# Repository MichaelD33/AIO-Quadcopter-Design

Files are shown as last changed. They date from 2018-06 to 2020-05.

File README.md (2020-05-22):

# AIO Quadcopter Design Files

__Disclaimer:__ This is a functional *yet unfinished* project. The information in this repository is provided without warranty or guaranteed funtionality. If you attempt to replicate this project, I am not responsible for any damages or failures associated with your work.

--- 

## This repository contains:

### 1. The schematics and Gerber files for the AIO quadcopter circuit board.

### 2. The 3D printed frame for the AIO quadcopter circuit board 
- (*version 0.4.1 strongly recommended*)

### 3. The Fusion360 assembly file for the AIO quadcopter.

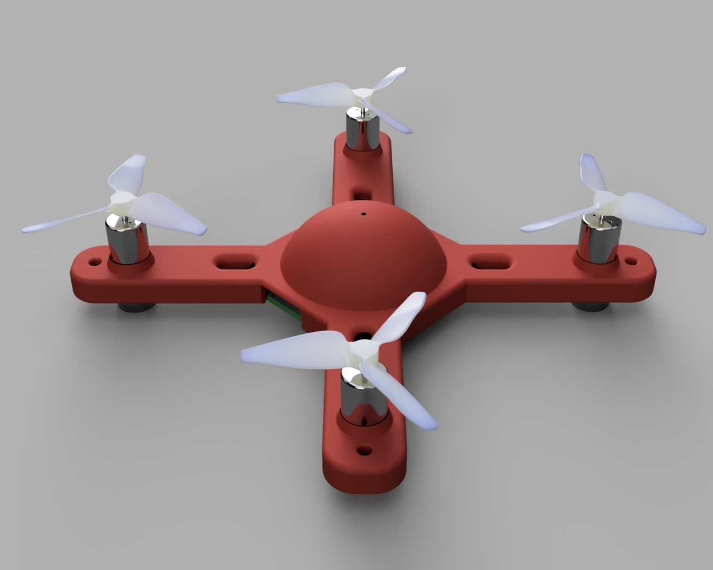
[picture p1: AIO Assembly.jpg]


### 4. The test jig folder containing all of the 3D printed parts necessary to build a test stand for the AIO quadcopter (version 0.3 and later) 
- (*The single axis version is strongly recommended over the legacy model*)
- This test stand is designed to operate using this [single axis control program](https://github.com/MichaelD33/SingleAxisController).

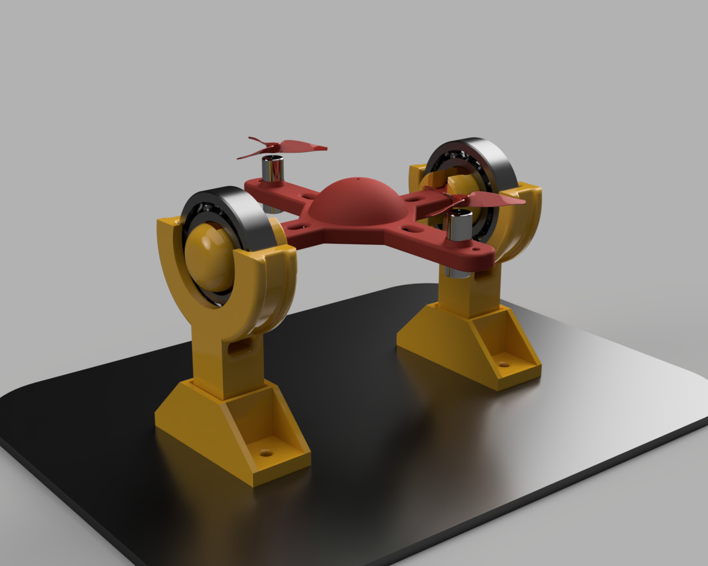
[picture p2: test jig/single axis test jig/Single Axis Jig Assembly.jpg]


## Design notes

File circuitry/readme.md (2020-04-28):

# AIO Quadcopter Circuit Board Design File Directory:

---

### Note: The use of the [AIO Quadcopter version 0.4.1](https://github.com/MichaelD33/AIO-Quadcopter-Design/tree/master/circuitry/version%200.4.1) circuit board design is highly recommended for new users attempting to follow this project.

*Prototype legacy designs are provided for reference only!*

---

## Version 0.4.1:



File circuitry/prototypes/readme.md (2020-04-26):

# AIO Quadcopter Legacy PCB Design Directory:

---

### Warning: This is a directory for archived designs. No further work will be done with these designs. Functionality or compatibility with future AIO designs is not ensured.

*These designs are provided as reference. The use of these designs is not recommended to anyone attempting this project.*

The use of the [AIO Quadcopter version 0.4.1](https://github.com/MichaelD33/AIO-Quadcopter-Design/tree/master/circuitry/version%200.4.1) 
circuit board design is highly recommended for new users attempting to follow this project.

---

## Directory Overview

### non-functional prototypes
	- Original PCB designs.
	- Used for early code development and hardware testing

### Version 0.3
	- First working revision of the PCB - This design removed the 5v buck/boost converter to decrease the overall weight; however, this resulted in the center of gravity being significantly offset from the center of the PCB. This results in a number of issues with the device's balance.

### Version 0.4
	- Fixed center of gravity
	- Replaced the 5V regulator (decreased efficiency due to the 3.3V regulator being powered by the 5V reg.)
	
### Version 0.4.1 (see link above)
	- Added flyback diode and reverse polarity protection mosfet.
	- 5V regulator and output pads (3.3V regulator still powered via 5V line)

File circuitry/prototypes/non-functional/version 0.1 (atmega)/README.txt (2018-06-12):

/* VERSION 1.0 README */

While the first circuit board design ultimately functioned, it required a number of modifications and did not satisfy my expectations for power consumption and efficiency. In addition, the motor drivers on this version of the quadcopter design came in a BGA package and were incredibly tiny and required significant patience and skill to properly solder. Finally, I also encountered issues with isolating the USB power from battery power which caused a number of issues later on when attempting to interface over serial or program the flight controller.

For these reasons, I would not recommend fabricating this version of the quadcopter. I have included it in the library for documentation purposes only.

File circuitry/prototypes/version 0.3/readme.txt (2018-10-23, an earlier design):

In an attempt to decrease the number of parts on the quadcopter circuit board, I removed the 5v regulator and connected the atmega directly to the 1S lipo voltage supply. In this process I changed the center of gravity significantly enough to offset the battery placement onto the arms. For this reason I would suggest working with version 0.4 over this iteration.

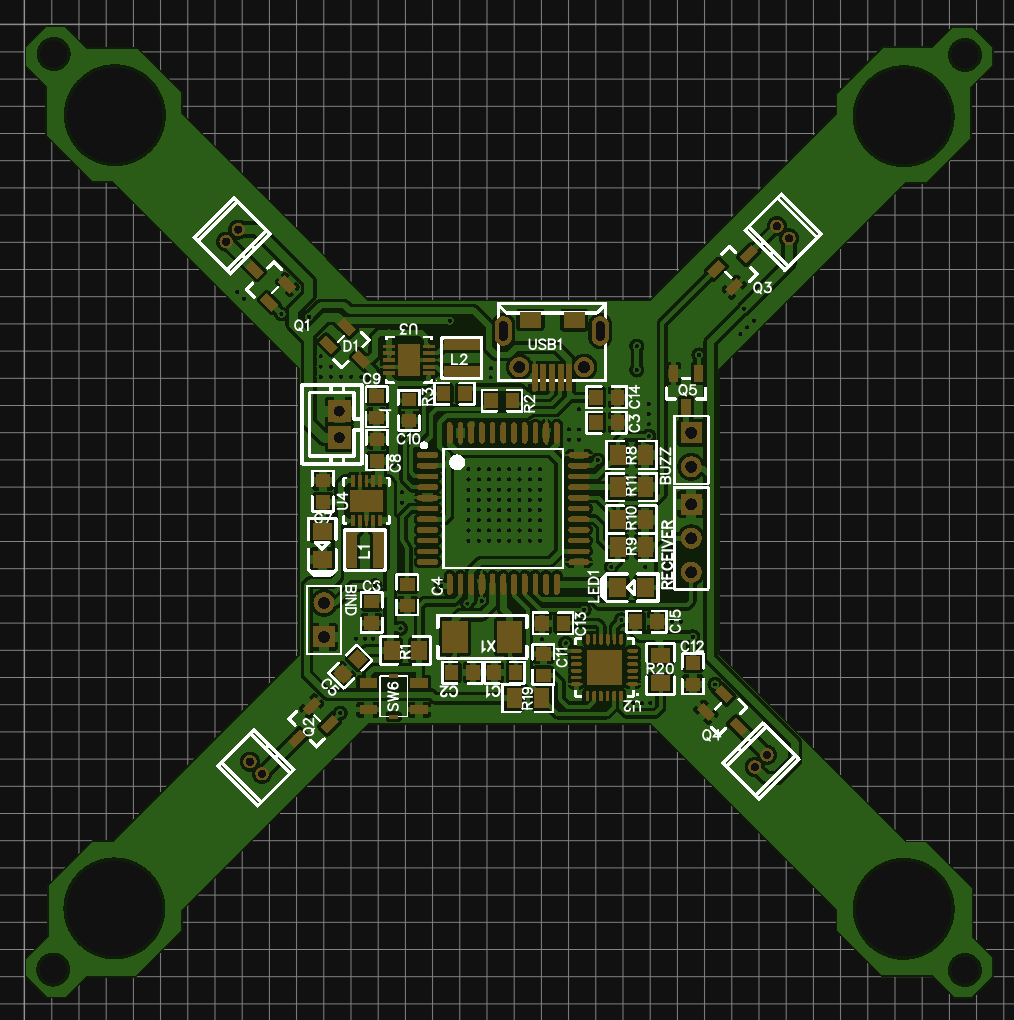
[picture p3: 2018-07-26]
circuitry/prototypes/version 0.4/AIO_32u4_v0.4.png

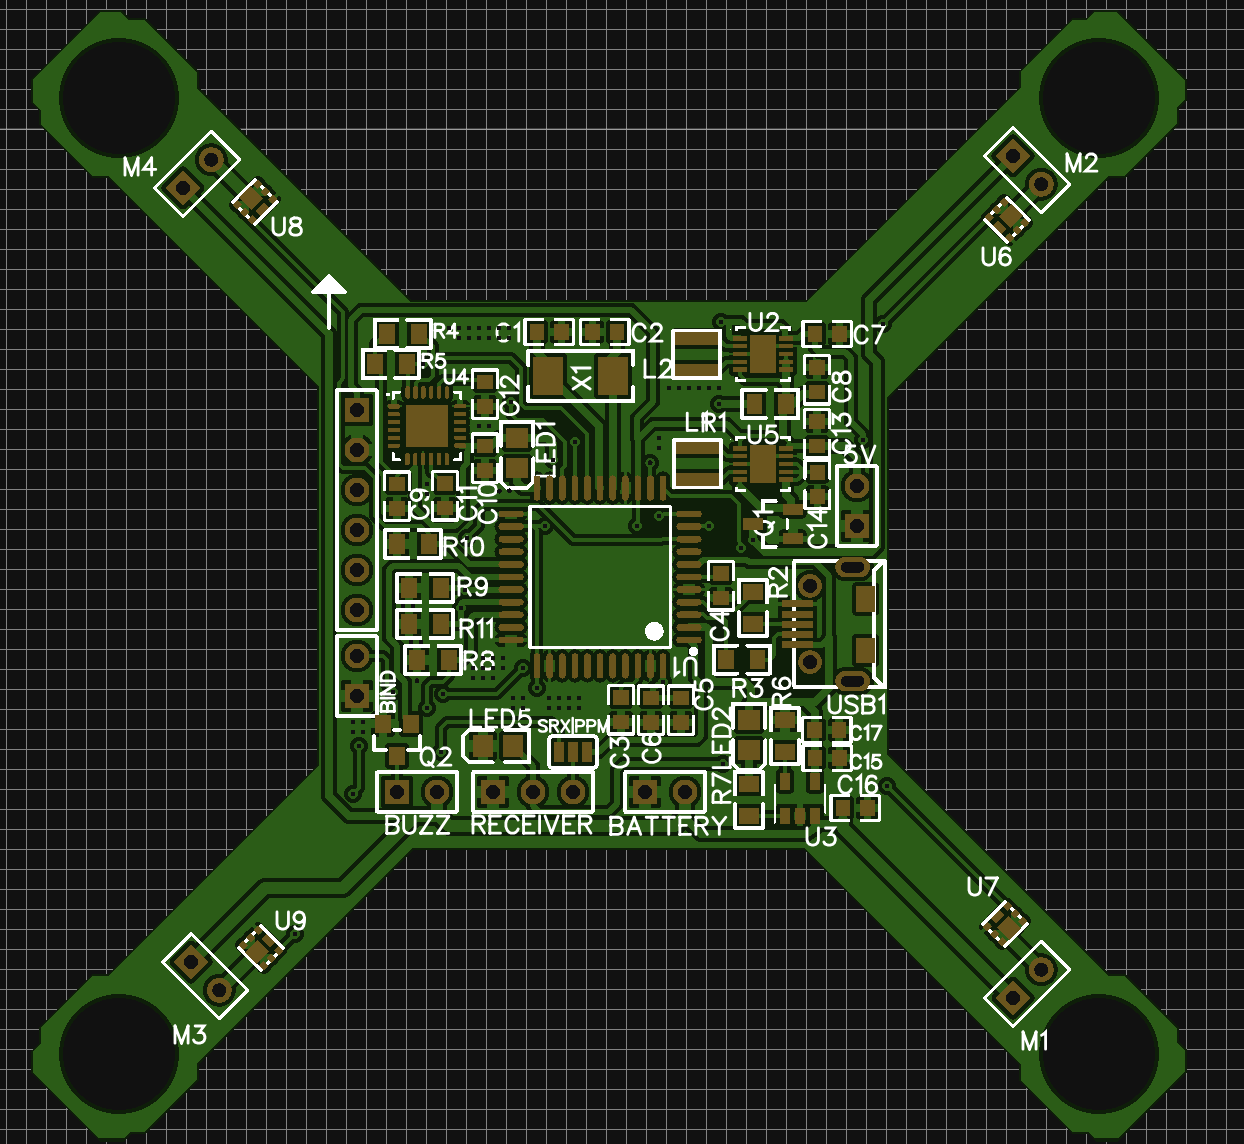
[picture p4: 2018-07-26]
circuitry/prototypes/non-functional/version 0.1 (atmega)/AIO_32u4_v0.1.png

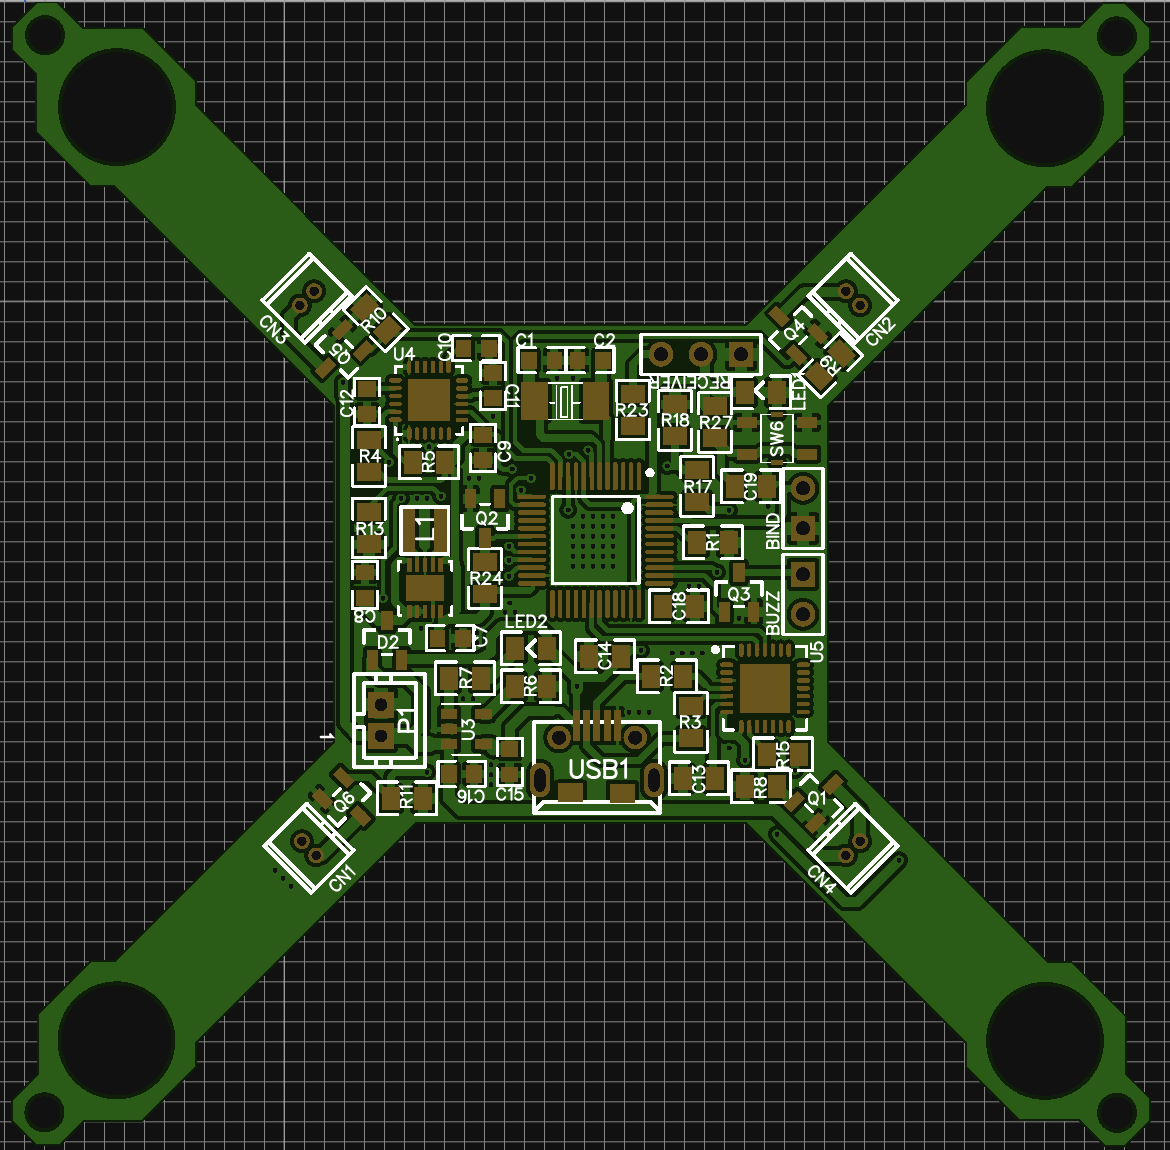
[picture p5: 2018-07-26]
circuitry/prototypes/non-functional/version 0.2 (stm32)/AIO_stm32_v0.2.png

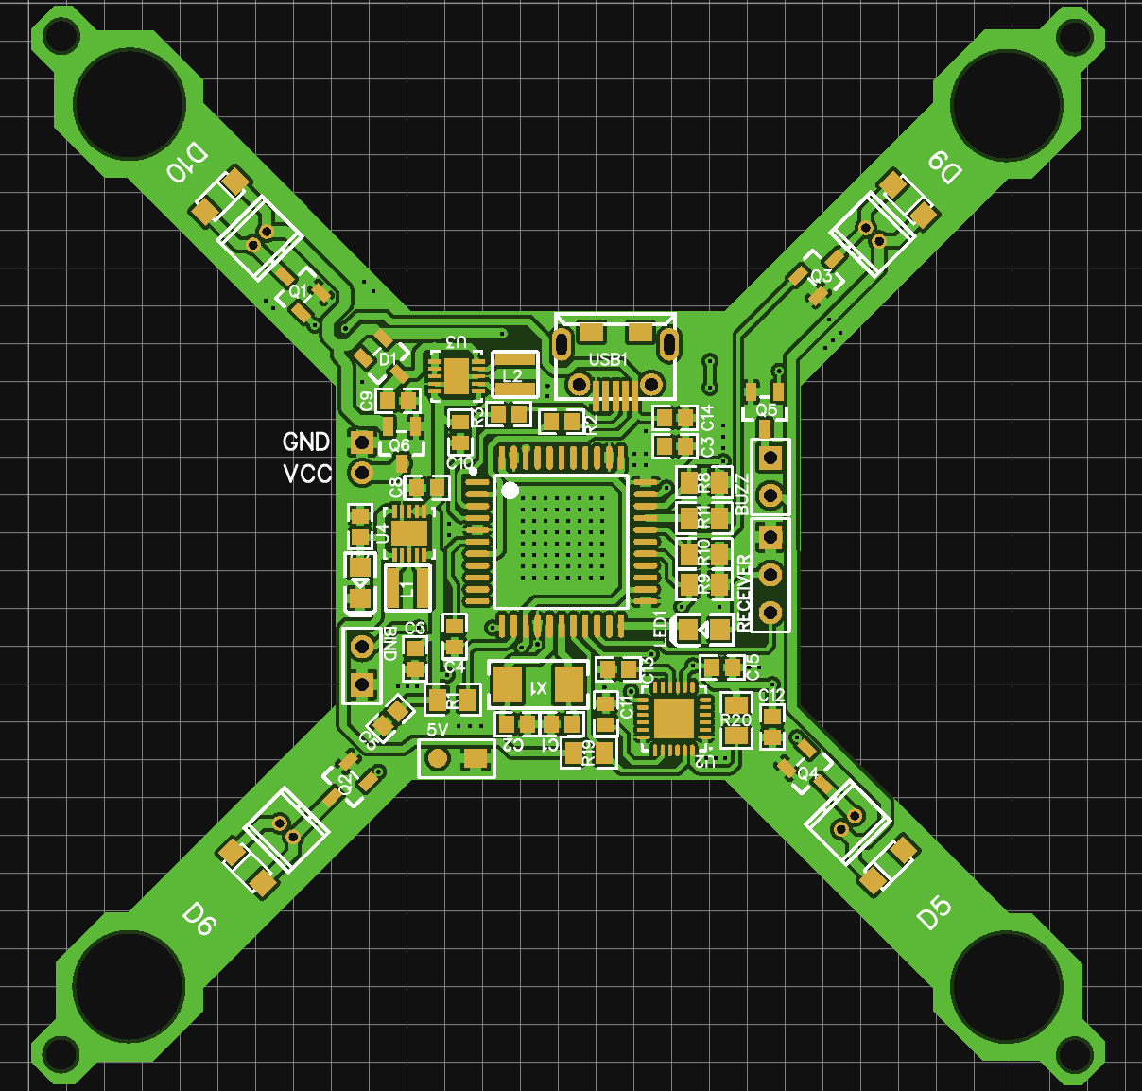
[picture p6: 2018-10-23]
circuitry/version 0.4.1/AIO_32u4_v0.4.1.png

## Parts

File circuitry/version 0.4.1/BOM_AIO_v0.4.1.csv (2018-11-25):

ID | Name | Designator | Footprint | Quantity | Manufacturer Part | Manufacturer | Supplier | Supplier Part | Mounted | LCSC Assembly
1 | ATMEGA32U4-AU | U1 | QFP-44_10X10X08P | 1 | ATMEGA32U4-AU | ATMEL | LCSC | C44854 | Yes
2 | 22pf | C1,C2 | 0603' | 2 | ? |  |  |  | Yes
3 | 10k | R1,R19,R20,R10,R11,R8,R9 | 0805' | 7 | ? |  |  |  | Yes
4 | 0.1uf | C3,C12,C13 | 0603' | 3 | ? |  |  |  | Yes
5 | 1uf | C4,C5,C6,C14 | 0603' | 4 | ? |  |  |  | Yes
6 | 16MHz | X1 | OSC-YSX-5032_2P | 1 | X503216MSD2GI | YXC | LCSC | C73355 | Yes
7 | MPU6050 | U2 | QFN-24_4X4X05P | 1 | MPU6050 | InvenSense | LCSC | C24112 | Yes | Yes
8 | 0.01uf | C15 | 0603' | 1 | ? |  |  |  | Yes
9 | 2.2nf | C11 | 0603' | 1 | ? |  |  |  | Yes
10 | TPS63001DRCR | U4 | DRC10-2400X1650TP | 1 | ? |  |  |  | Yes
11 | NR3015T2R2M | L1,L2 | 3.0*3.0*1.5MM | 2 | NR3015T2R2M | TAIYO YUDEN | LCSC | C86423 | Yes
12 | 10uf | C7,C8,C10,C9 | 0603' | 4 | ? |  |  |  | Yes
13 | E6C0805UR | LED3,LED1 | LED-0805 | 2 | E6C0805UR | LCSC | LCSC | C2295 | Yes
14 | TPS63002DRCR | U3 | DRC10-2400X1650TP | 1 | ? |  |  |  | Yes
15 | MICRO USB 5S B | USB1 | MICRO-USB-1 | 1 | micro USBFemale | ValuePro | LCSC | C10418 | Yes
16 | Buzzer | BUZZ | HDR-2X1/2.54 | 1 | Header-Male-2.54_1x2 | LCSC | LCSC | C36717 | Yes
17 | RECEIVER | RECEIVER | HDR-3X1/2.54 | 1 | Header-Male-2.54_1x3 | LCSC | LCSC | C49257 | Yes
18 | BIND | BIND | HDR-2X1/2.54 | 1 | Header-Male-2.54_1x2 | LCSC | LCSC | C36717 | Yes
19 | SI2302CDS-T1-E3 | Q4,Q2,Q3,Q1 | SOT-23(SOT-23-3) | 4 | SI2302CDS-T1-E3 | VISHAY | LCSC | C141544 | Yes
20 | 1.25T-2P-DP | CN4,CN2,CN3,CN1 | 1.25T-2P-DP | 4 | 1.25T-2P-DP | HRO | LCSC | C145940 | Yes
21 | BAT54C | D1 | SOT-23(SOT-23-3) | 1 | BAT54C | CJ | LCSC | C2135 | Yes
22 | MMBT3906LT1G | Q5 | SOT-23(SOT-23-3) | 1 | MMBT3906LT1G | ON | LCSC | C53444 | Yes
23 | 22 | R2,R3 | 0603' | 2 | ? |  |  |  | Yes
24 | S07J-GS08 or | S07M-GS08 | D2,D3,D4,D5 | DO-219AB | 4 | S07J-GS08 | VISHAY | LCSC | C145004 | Yes
25 | Header-Male-2.54_1x2 | 5V | HDR-2X1/2.54 | 1 | 826629-2 | TE Connectivity | LCSC | C86471 | Yes
26 | SI2301CDS-T1-GE3 | Q6 | SOT-23(SOT-23-3) | 1 | SI2301CDS-T1-GE3 | VISHAY | LCSC | C10487 | Yes | Yes
27 | VCC | VCC,GND | _PIN | 2 | New SchematicLib |  |  | undefined | Yes

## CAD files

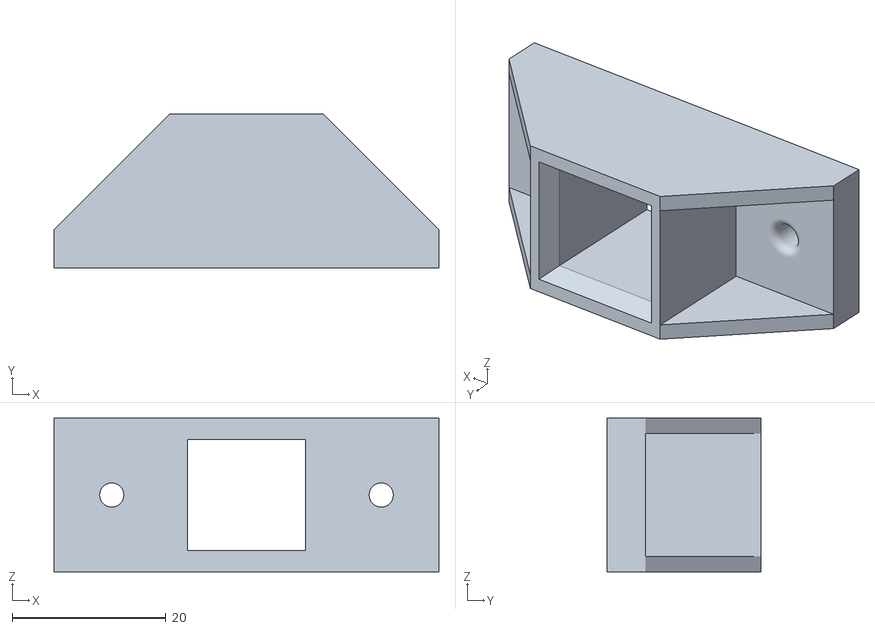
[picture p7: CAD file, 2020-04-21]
test jig/single axis test jig/Base Mount.stl
50.0 x 20.0 x 20.0

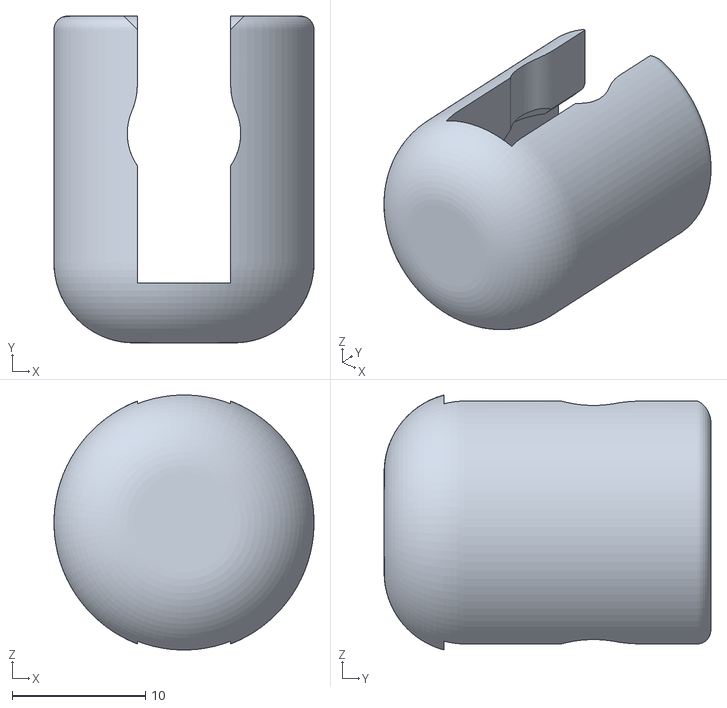
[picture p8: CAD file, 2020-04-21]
test jig/single axis test jig/Bearing Clip.stl
19.5 x 24.5 x 19.1

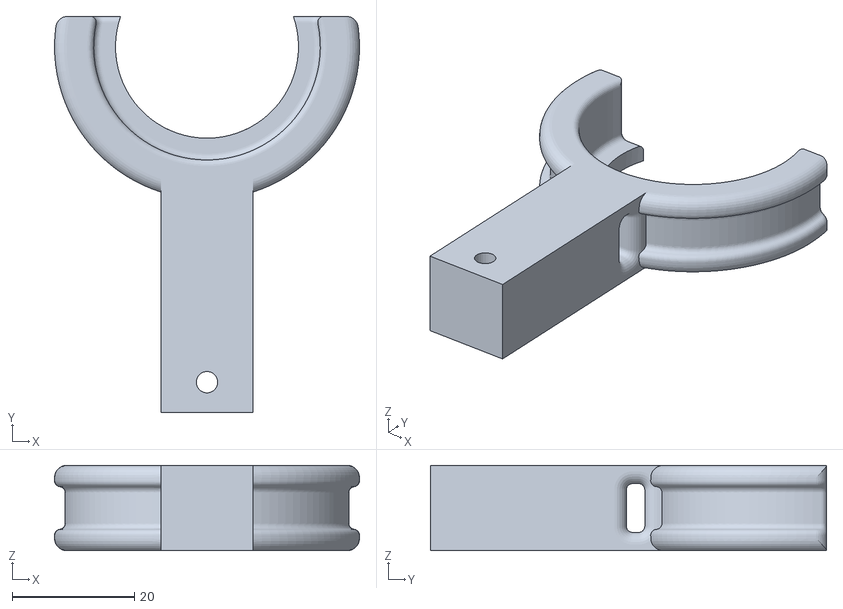
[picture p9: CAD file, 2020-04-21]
test jig/single axis test jig/Mounting Post.stl
50.0 x 65.0 x 14.0

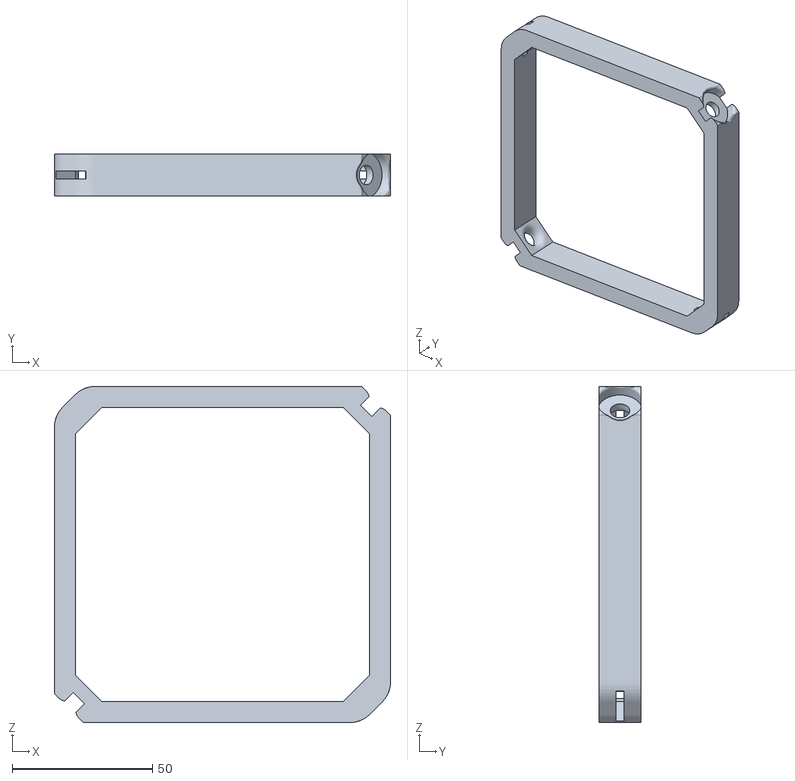
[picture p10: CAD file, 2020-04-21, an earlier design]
test jig/legacy test jig/Full Mount Test.stl
120.0 x 15.0 x 120.0

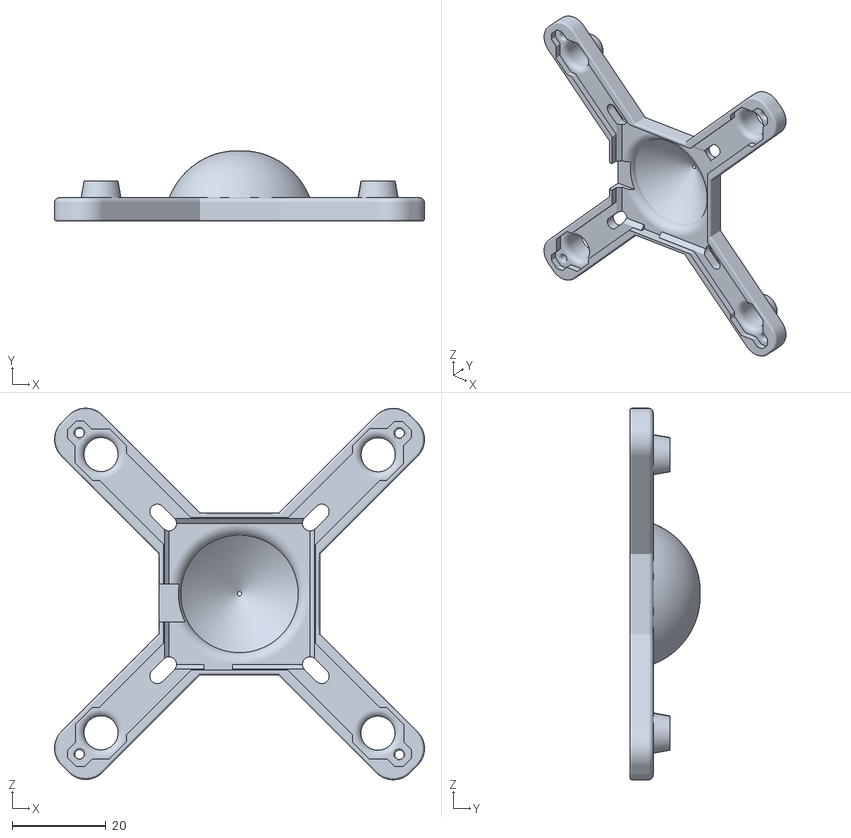
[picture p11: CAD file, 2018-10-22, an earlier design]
3D printed frame/legacy designs/AIO Top Mount Frame v1.stl
78.8 x 15.0 x 79.1

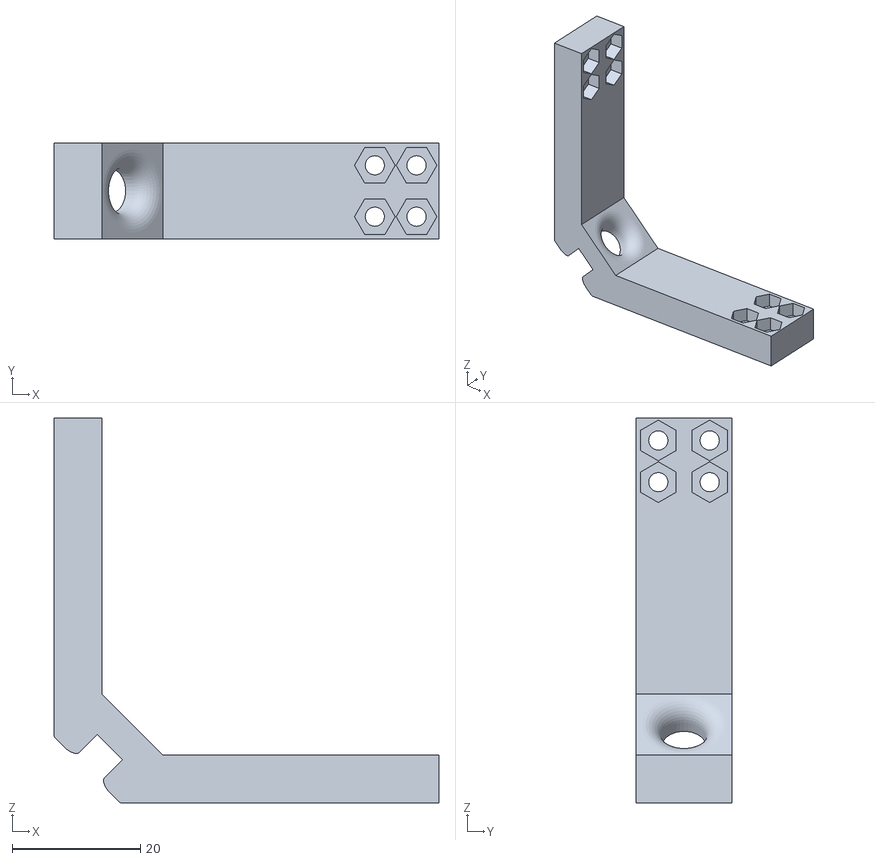
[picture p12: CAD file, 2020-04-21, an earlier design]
test jig/legacy test jig/Large Corner Bracket - Dual.stl
60.0 x 15.0 x 60.0

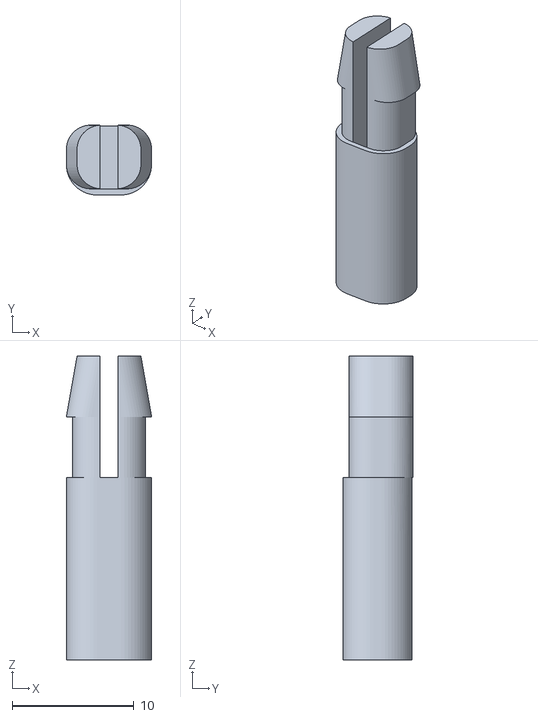
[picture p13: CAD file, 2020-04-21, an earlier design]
test jig/legacy test jig/quadcopterMountingClip_Bearing.stl
7.01 x 5.75 x 25.0

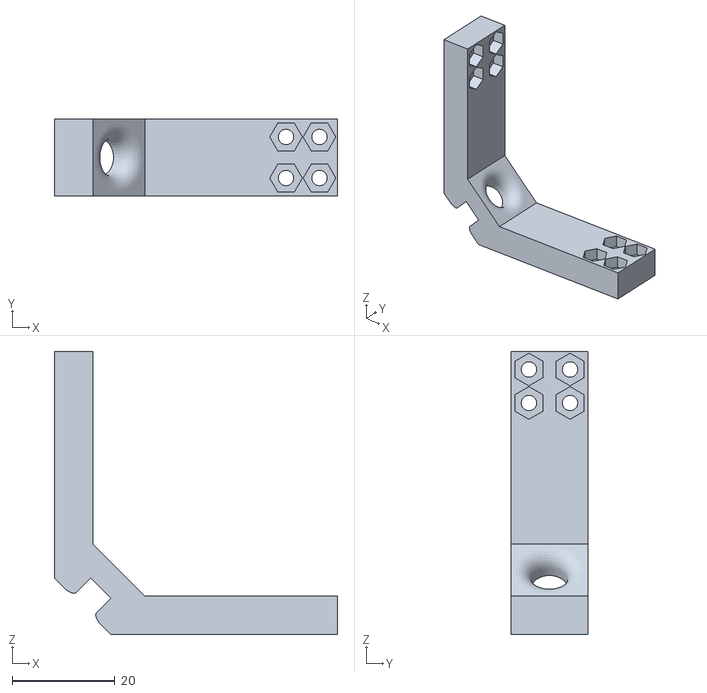
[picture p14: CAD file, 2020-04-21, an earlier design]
test jig/legacy test jig/Corner Bracket Dual Mounting Hole.stl
55.0 x 15.0 x 55.0

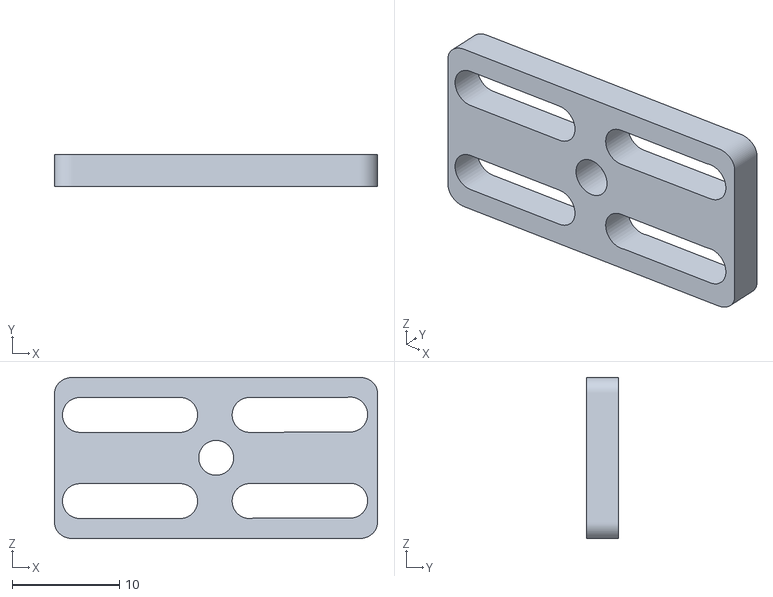
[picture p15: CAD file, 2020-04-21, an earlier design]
test jig/legacy test jig/Expanding Bracket.stl
30.1 x 3.00 x 15.0

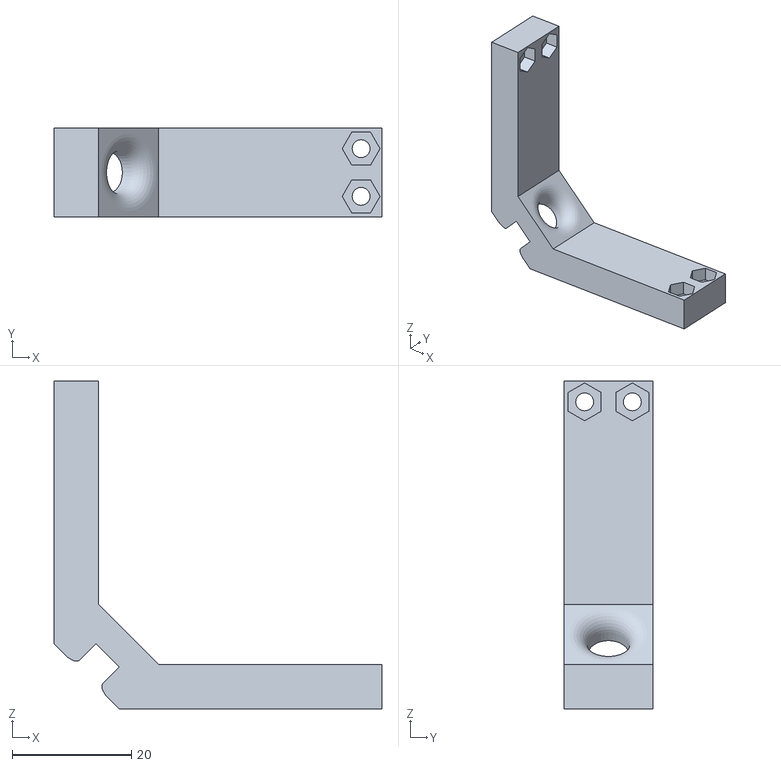
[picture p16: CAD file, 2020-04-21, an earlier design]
test jig/legacy test jig/PID Expanding Mount.stl
55.0 x 15.0 x 55.0

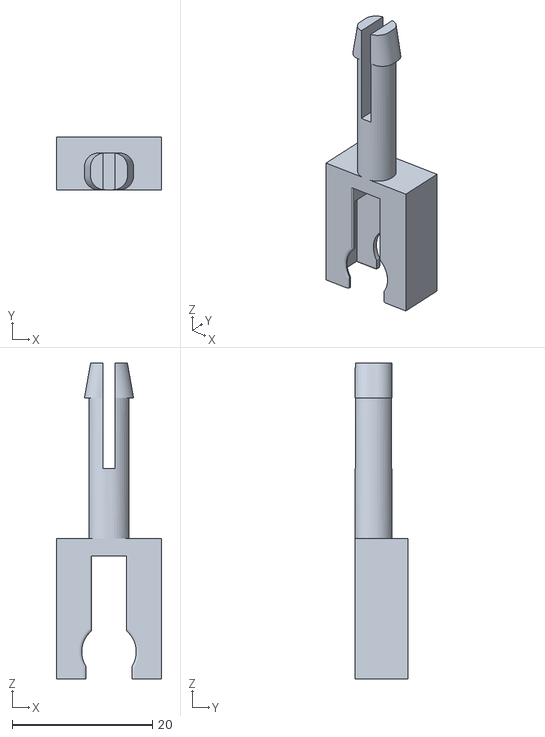
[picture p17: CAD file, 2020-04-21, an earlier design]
test jig/legacy test jig/innerAxisMountingPin.stl
15.0 x 7.50 x 45.0

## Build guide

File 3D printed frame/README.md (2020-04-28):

# AIO 3D Printed Frame

---

This 3D printed frame serves as support for the AIO quadcopter PCB. 
The frame was added for two main purposes: vibration dampening and rigidity.

Assembly:

- The quadcopter frame is attached to the PCB using standard [M2 x 6mm](https://www.mcmaster.com/92000a013) screws. 
These screws attach to the quadcopter PCB through the mounting holes at the end of each motor arm. 
The screws are held in place using [M2 nuts](https://www.mcmaster.com/93800a300).

- The frame also features cutouts for vibration dampening components. 



- [M2 O-Rings](https://www.banggood.com/20-PCS-O-rings-Vibration-Isolation-Flight-Controller-Protection-Rubber-Band-Green-White-for-RC-Drone-p-1174651.html?ID=521800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)
or [M2 O-Rings – Option 2](https://www.mcmaster.com/9262k568)

- [Adhesive Foam Pads](https://www.banggood.com/10Pcs-URUAV-3M-Double-Sided-Foam-Adhesive-Tapes-Pad-Square-Strip-for-Gyro-RC-Models-p-1353765.html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)
or [Adhesive Foam – Option 2](https://www.mcmaster.com/75785t13)

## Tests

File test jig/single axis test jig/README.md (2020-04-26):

# Single Axis Test Jig Design



---

This testing jig is designed to allow the quadcopter to move freely along a singular axis of rotation. 
This setup configuration allows for the user to test the quadcopter's behavior and tune the PID controller without the
quadcopter flying away. Addionally, given that the motion is restricted to a singular axis, PID tuning is simplified by only focusing
on the singular axis of rotation (as opposed to the legacy test jig design, which allows for movement on all axes when properly configured).

---

__Dependancies:__

- This jig requires two of each 3D printed component, one set for each arm of the quadcopter. 

- Two bearings are also required for the device to be to rotate freely along the axis of rotation. The test jig is designed to work with [20x37 mm bearings](https://www.mcmaster.com/5972k168).

- Mounting the quadcopter circuit board to the jig requires the 3D printed [AIO frame](https://github.com/MichaelD33/AIO-Quadcopter-Design/blob/master/3D%20printed%20frame/AIO%20Frame%20Refined.stl).

- Finally, of course, the [AIO quadcopter circuit board](https://github.com/MichaelD33/AIO-Quadcopter-Design/tree/master/circuitry/version%200.4.1) is required— this is the main control board for the quadcopter.

---

__Program Changes:__

- This setup utilizes a custom control program to test and tune the quadcopter. This program may be found in the [SingleAxisController](https://github.com/MichaelD33/SingleAxisController/) repository.

Read more about the specific changes on the single axis controller repository.

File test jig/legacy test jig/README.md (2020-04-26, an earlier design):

# Legacy Test Jig

---

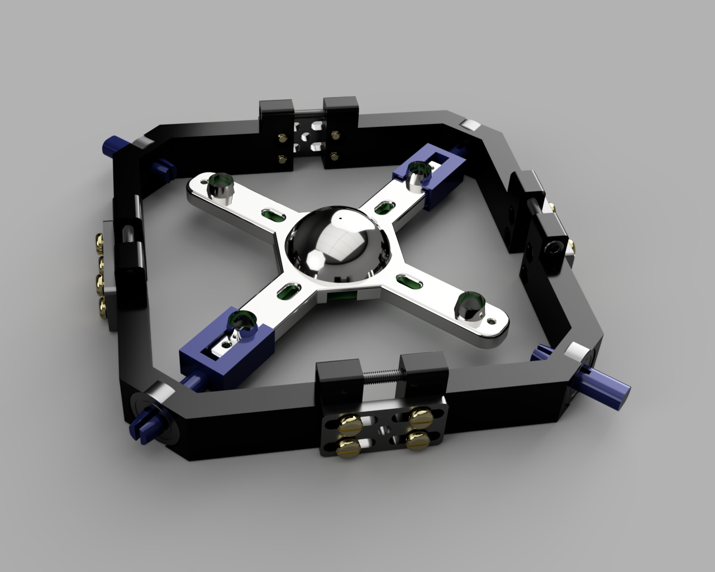
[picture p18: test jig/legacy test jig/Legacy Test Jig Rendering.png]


### Warning: This is an archived design. No further work will be done with this design. Compatibility with future AIO designs is not ensured.

*These designs are provided as reference. The use of these designs is not recommended to anyone attempting this project on their own.*

### Design update: 

The use of the [Single Axis Test Jig](https://github.com/MichaelD33/AIO-Quadcopter-Design/tree/master/test%20jig/single%20axis%20test%20jig) 
design is highly recommended for new users attempting to follow this project.

---

__Purpose:__

The creation of this test jig is described in an article I published on the [Ultimaker website](https://ultimaker.com/learn/how-the-tools-we-use-influence-the-designs-we-make)— 
see: "__Tools in testing__".

The quadcopter uses information from the sensors to calculate how fast to spin the motors in order to move to 
a certain location. This process is handled by an algorithm known as a PID controller. Before the quadcopter can fly, this controller needs to be configured through laborious testing, and figuring out where 
to start can be fairly daunting. Furthermore, the guess-and-check method usually causes the quadcopter to go crashing into the 
wall. This caused me to wonder, how might I control and analyze the movement of the quadcopter without it flying away and 
crashing into the wall?

Introducing, the testing jig. This contraption allows the user to test the quadcopter without worrying that the device will break
from colliding with the wall. 

[See an example of this test jig in action](http://delaney.nyc/wp-content/uploads/2020/04/PIDTestJig3.gif)

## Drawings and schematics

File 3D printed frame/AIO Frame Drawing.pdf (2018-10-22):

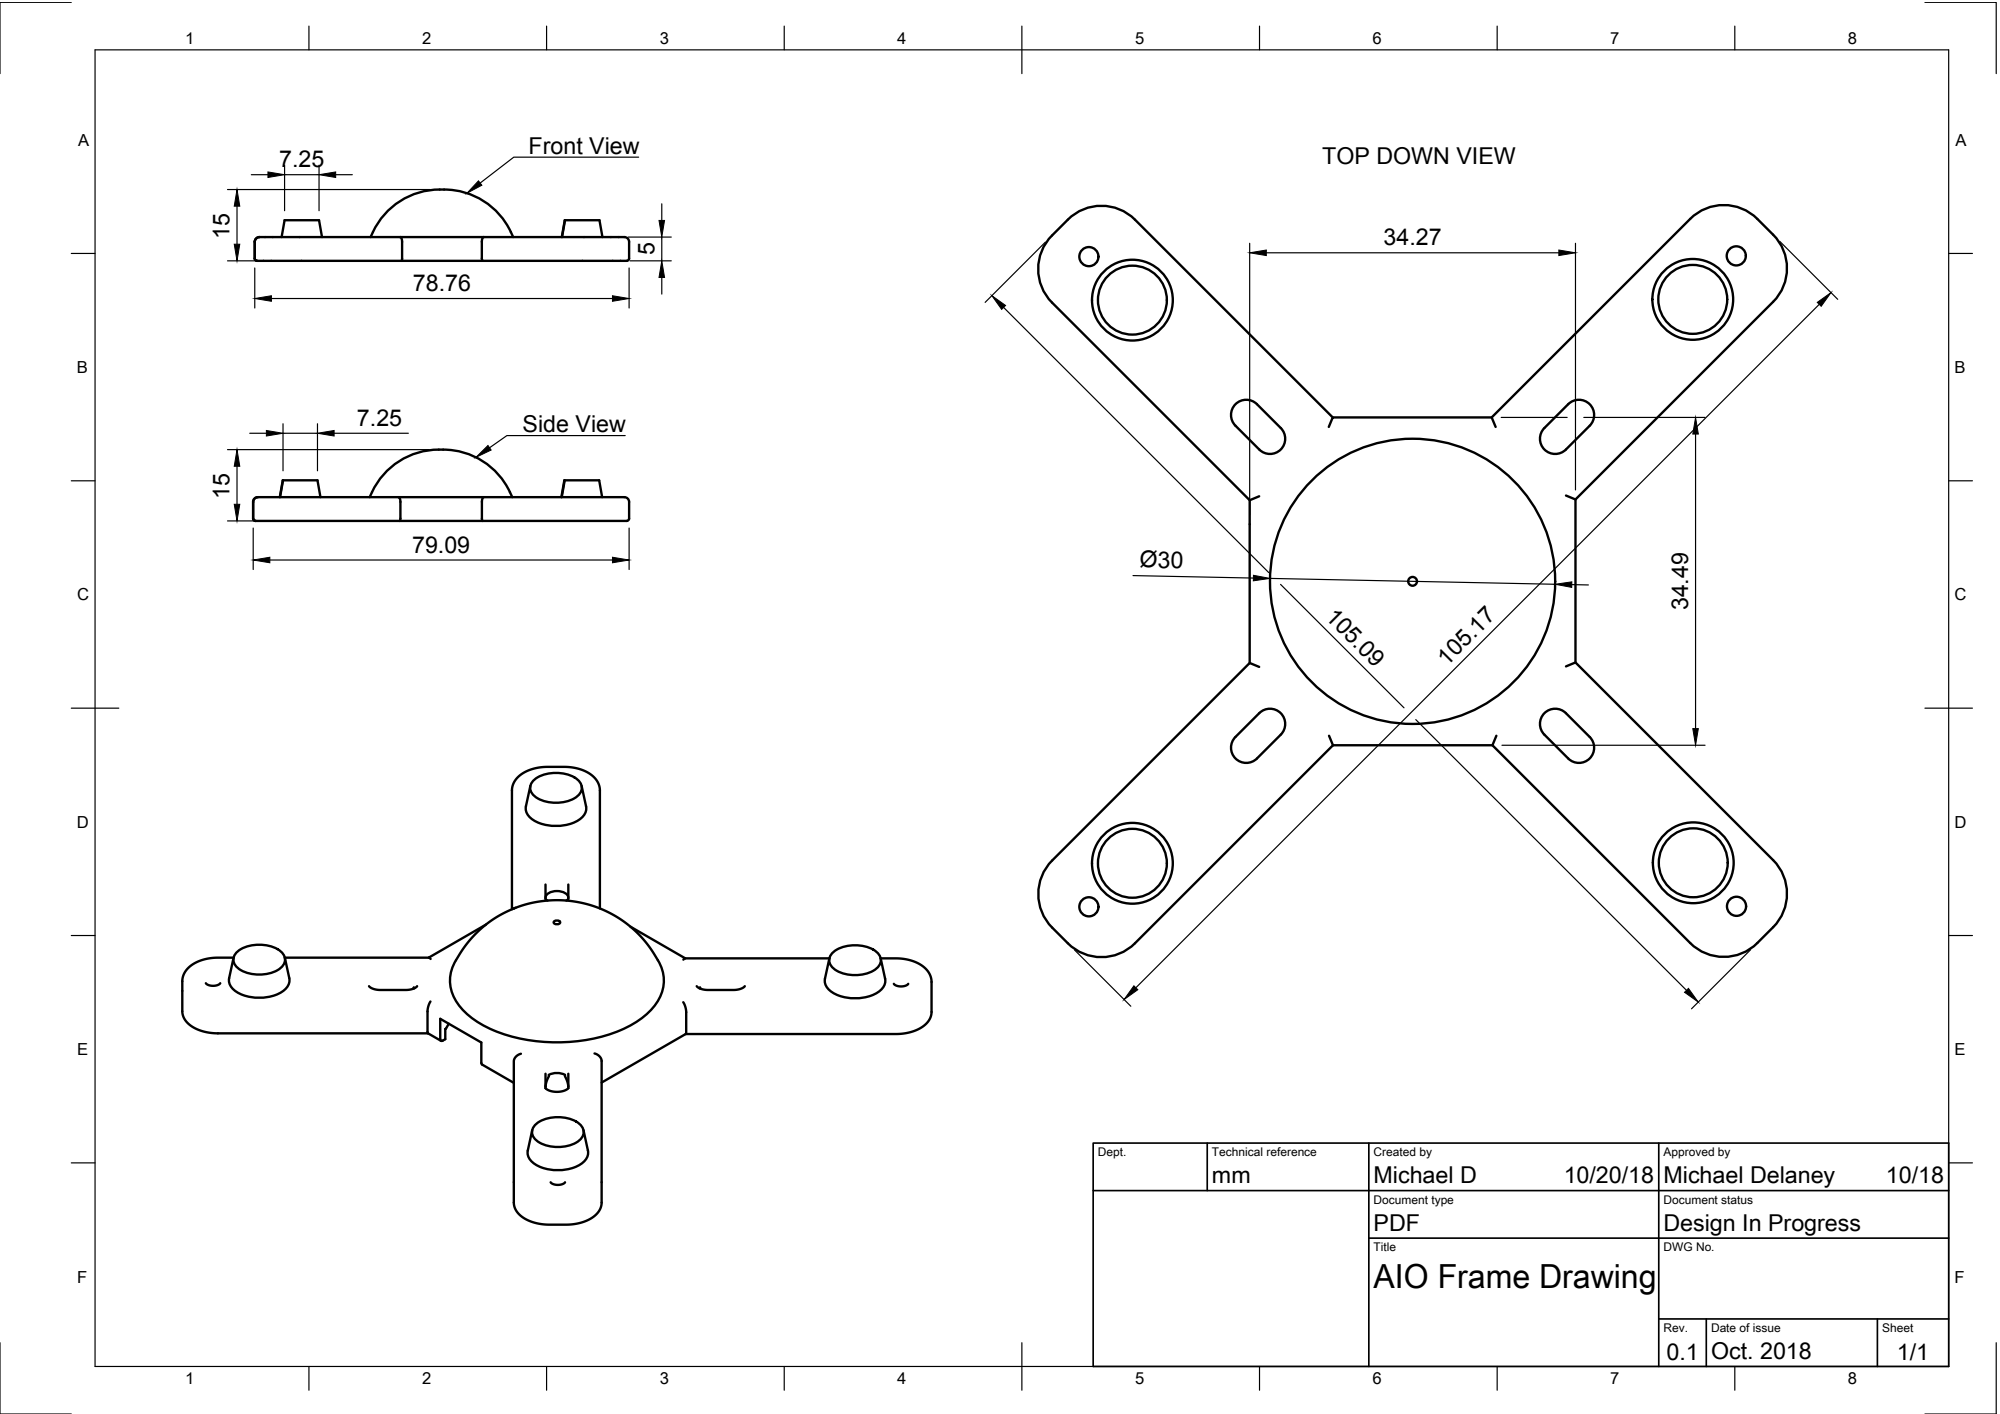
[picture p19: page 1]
Front View; Side View

TOP DOWN VIEW

Dept. | Technical reference mm | Created by Michael D 10/20/18 | Approved by Michael Delaney 10/18

Document type PDF | Document status Design In Progress

Title AIO Frame Drawing | DWG No.

Rev. 0.1 | Date of issue Oct. 2018 | Sheet 1/1

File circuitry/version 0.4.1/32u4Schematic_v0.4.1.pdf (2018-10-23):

+3.3V +3.3V

## VCC

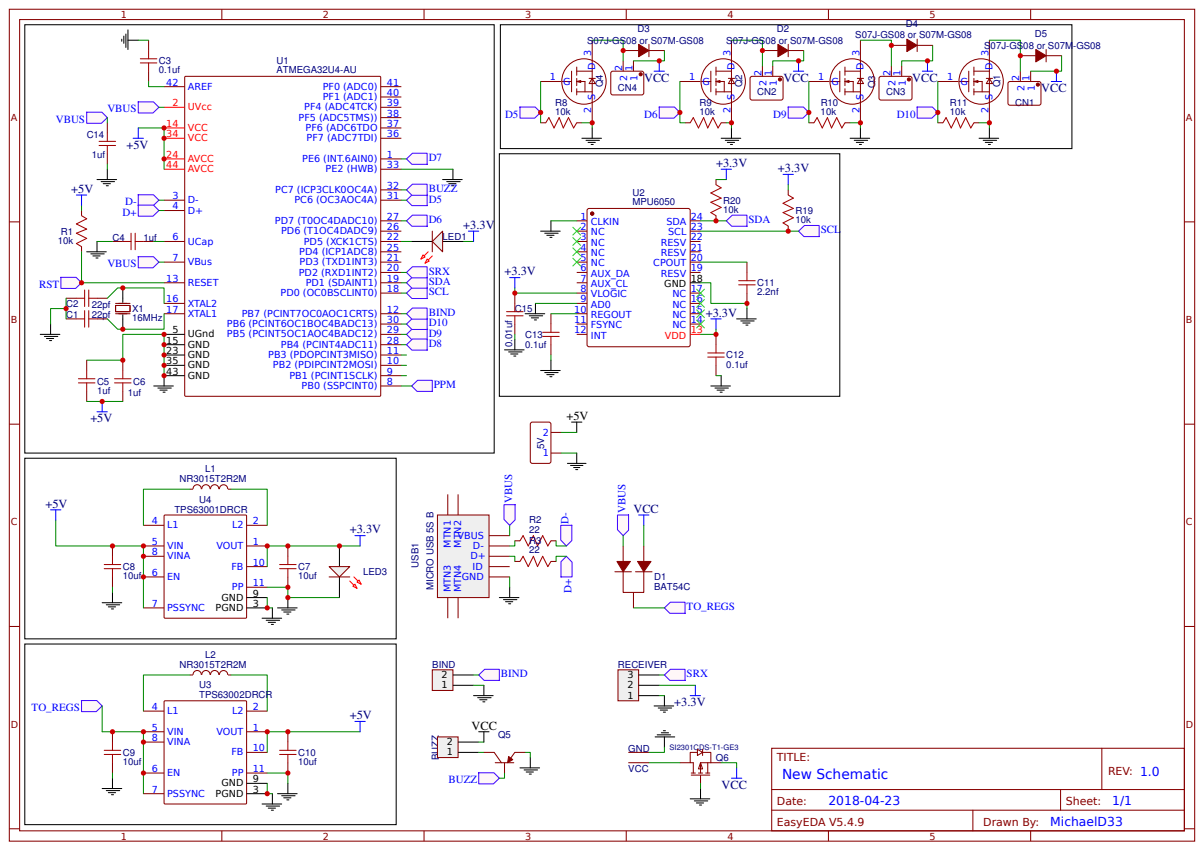
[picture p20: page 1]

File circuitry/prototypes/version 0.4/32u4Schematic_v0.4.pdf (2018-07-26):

+3.3V +3.3V

## VCC

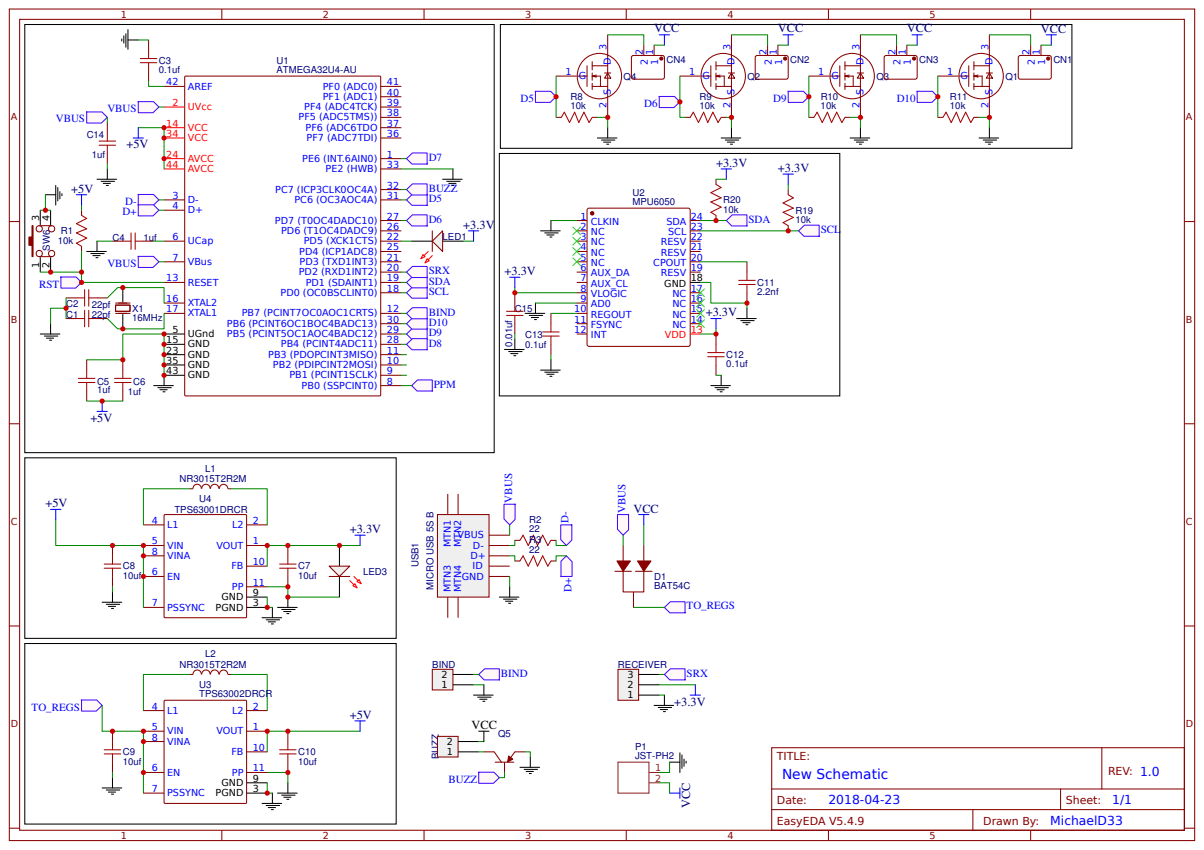
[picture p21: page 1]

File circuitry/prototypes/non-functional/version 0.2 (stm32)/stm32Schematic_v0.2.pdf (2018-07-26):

## MPU6050

U4

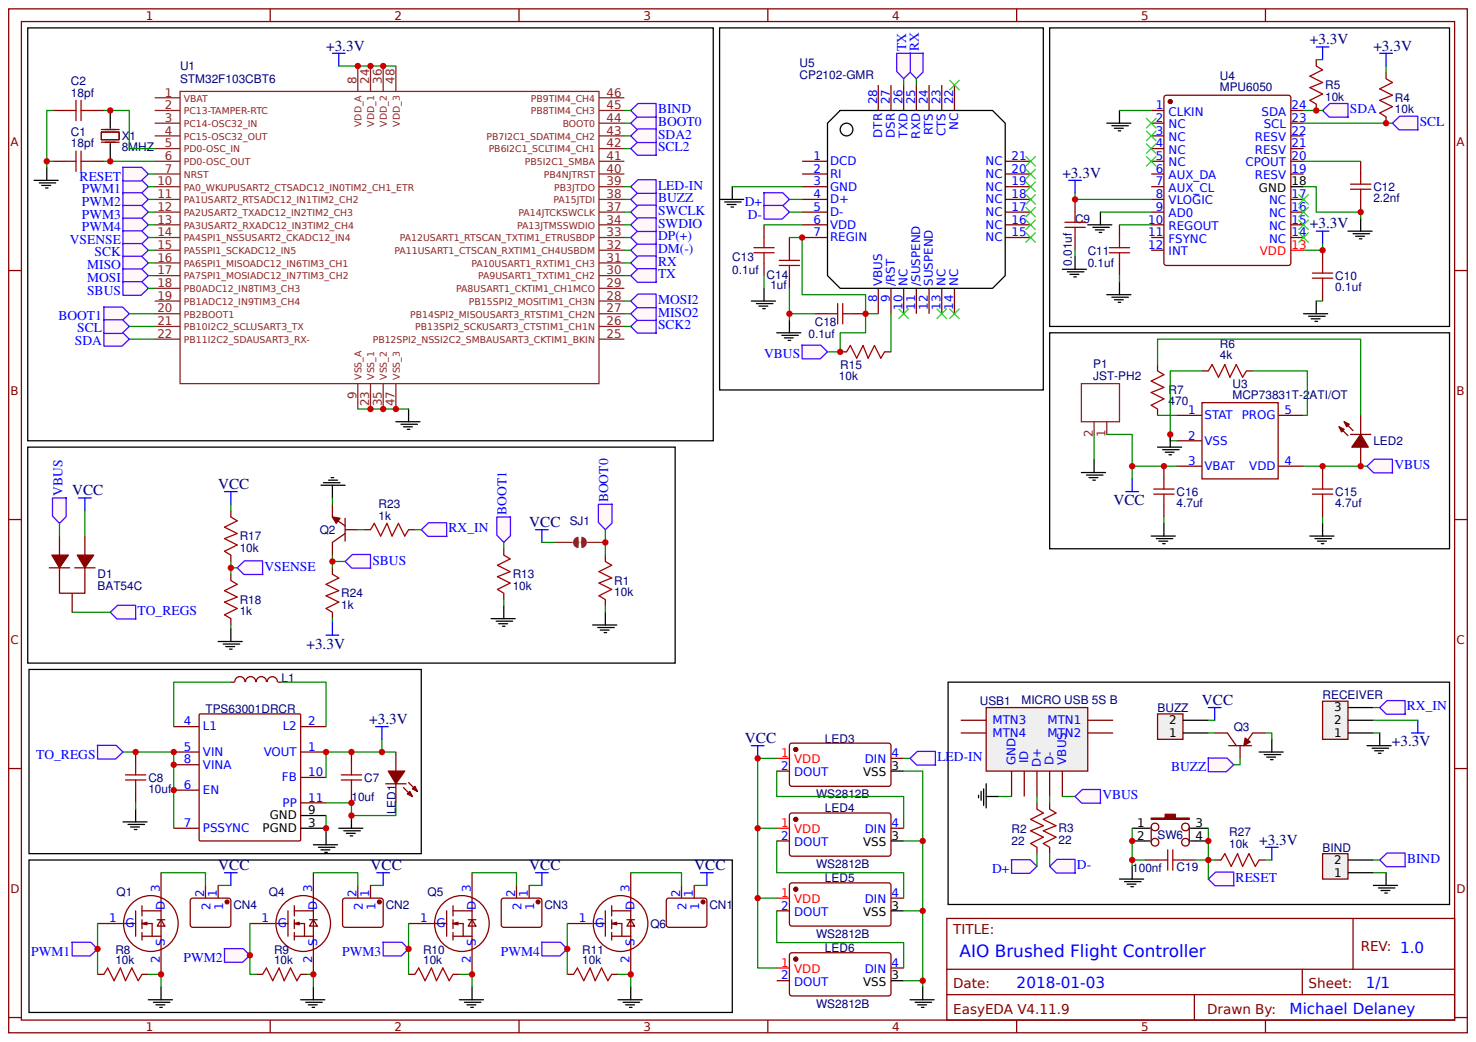
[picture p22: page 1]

NC 22 CTS 23 RTS 24 RXD 25 TXD 26 DSR 27 DTR 28

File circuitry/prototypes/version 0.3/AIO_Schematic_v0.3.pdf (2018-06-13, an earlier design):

+3.3V +3.3V

## VCC

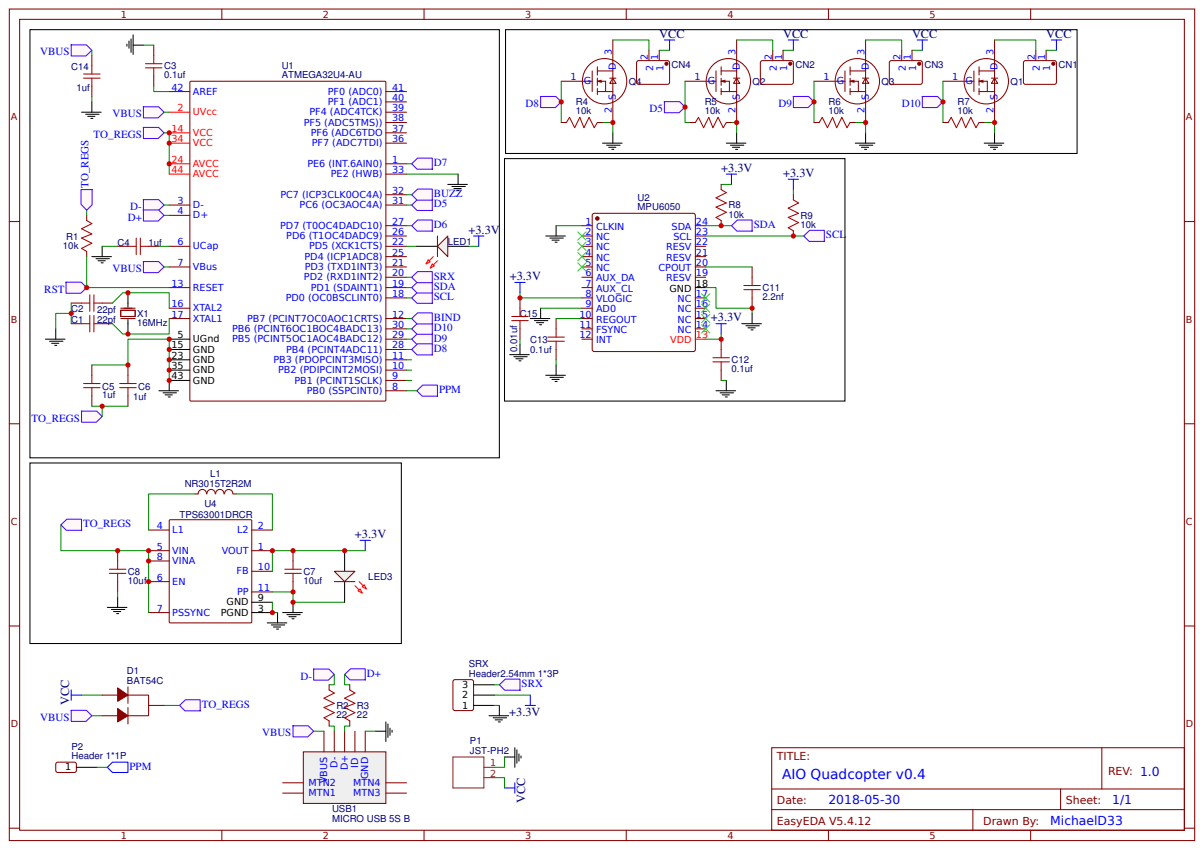
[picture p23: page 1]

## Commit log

2018-06-13 Added version 1 through 3 design files with schematics
    - no schematic for version 1
    - readme for version 1
    [Gerber_BoardOutline.GKO, Gerber_BottomLayer.GBL, Gerber_BottomSilkLayer.GBO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]
2018-07-26 added micro brushless flight control boards + file structuring
    [Gerber_BoardOutline.GKO, Gerber_BottomLayer.GBL, Gerber_BottomPasteMaskLayer.GBP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]
2018-07-26 added images and corrected structuring
    [Gerber_BoardOutline.GKO, Gerber_BottomLayer.GBL, Gerber_BottomSilkLayer.GBO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]
2018-09-12 fixed ground plane on motor 3 and changed pinout to PWM pin for proper motor control
    [Gerber_BoardOutline.GKO, Gerber_BottomLayer.GBL, Gerber_BottomSolderMaskLayer.GBS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]
2018-09-12 fixed ground planes on motor outputs
    [Gerber_BoardOutline.GKO, Gerber_BottomLayer.GBL, Gerber_BottomSilkLayer.GBO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]
2018-09-12 increased motor trace thickness for VCC input
    [Gerber_BoardOutline.GKO, Gerber_BottomLayer.GBL, Gerber_BottomSilkLayer.GBO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]
2018-10-22 added 3D printed frame drawing
2018-10-22 added updated frame and moved legacy design to dedicated folder
    [AIO_PCB_FRAME_v0.1.stl]
2018-10-23 file restructuring and added verion 0.4.1 circuit
    [Gerber_BoardOutline.GKO, Gerber_BottomLayer.GBL, Gerber_BottomPasteMaskLayer.GBP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]
2018-11-25 added BOM
    [BOM_AIO_v0.3.csv, BOM_AIO_v0.4.1.csv]
2020-04-21 re-ordered file structure
    [AIO_PCB_FRAME_v0.1.stl, BOM_AIO_v0.3.csv, BOM_AIO_v0.4.1.csv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]
2020-04-21 added pdf drawing of the AIO frame
2020-04-21 added updated STL file of the AIO frame
2020-04-21 added legacy designs for reference
    [AIO Top Mount Frame v1.stl]
2020-04-21 file restructuring
    [BOM_AIO_v0.3.csv, BOM_AIO_v0.4.1.csv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]
2020-04-21 added assembly model
2020-04-21 added assembly image
2020-04-21 added legacy test jig 3D models
    [Corner Bracket Dual Mounting Hole.stl, Expanding Bracket.stl, Full Mount Test.stl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]
2020-04-21 added single axis jig 3D models
    [Base Mount.stl, Bearing Clip.stl, Mounting Post.stl]
2020-04-21 added single axis jig assembly image
2020-04-28 create README for 3D printed frame
    - Added basic assembly instructions and links to the parts needed for the 3D printed frame
